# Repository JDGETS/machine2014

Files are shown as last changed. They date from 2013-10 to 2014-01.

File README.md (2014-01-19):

Machine des Jeux de Génie 2014
===========

Le logiciel de la machine est développer entièrement en Python, est exécuté sur un BeagleBone Black avec Ångström et utilise la librairie Adafruit.BBIO pour le contrôle des GPIO/ADC/PWM.

Les sources sont disponible dans /code/src/.

Le camion exécute /code/src/main_camion.py et la trieuse /code/src/main_collector.

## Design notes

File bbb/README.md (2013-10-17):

BeagleBone Black
================

SD card setup:
--------------

We use the Ubuntu Raring 13.04 image from [this site](http://www.armhf.com/index.php/download/)

```
cd /tmp
wget http://s3.armhf.com/debian/raring/bone/ubuntu-raring-13.04-armhf-rootfs-3.8.13-bone20.img.xz
xz -cd ubuntu-raring-13.04-armhf-3.8.13-bone20.img.xz > /dev/*YOURDEVICE*
```
ATTENTION: ne vous trompez pas de device!

C'est possible que `sudo su -` soit necessaire pour la derniere commande.

First Boot:
-----------

1. Figure out the IP address of the device. On the JDG-Machine network, goto http://192.168.1.1/ and look for computer named "ubuntu-armhf".
2. Boot the device; you should be able to connect to SSH with username *ubuntu* & password *ubuntu*
3. Do the "Ubuntu Setup" procedure below (only once).

Ubuntu Setup:
-------------

1. Go to `/etc/network/interfaces` and uncomment the wlan0 lines at the bottom. Setup the wifi name (JDG-Machine) and password.
2. Download the Machine 2014 repo: `git clone https://github.com/JDGETS/machine2014.git`
3. $ cd machine2014/bbb
4. $ make install-deps
5. $ install vim and screen from apt-get : sudo apt-get install screen vim
6. copy .bashrc and .screenrc from the scripts folder to the home directory
7. add your public key and copy the authorized_keys to ~/.ssh/ dont forget to commit the changes to authorized_keys
8. copy interfaces file from the script folder to /etc/network/
9. $ git config --global user.email "machine-jdg-2014@googlegroups.com"

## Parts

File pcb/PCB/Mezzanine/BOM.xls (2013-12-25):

Designator | Description | LibRef | Quantity | Value | Supplier Part Number 1 | Supplier Unit Price 1 | Supplier Subtotal 1
C1, C6, C10 | CAP CER 1UF 50V 10% X7R 0805 | Cap-Samsung-CL-50V-1.0uF-0805-10% | 3 | 1.0uF | 1276-1029-1-ND | 0,11 | 0,33
C2, C7, C11 | CAP CER 2.2UF 50V 10% X5R 0805 | Cap-Samsung-CL-50V-2.2uF-0805-10% | 3 | 2.2uF | 1276-2409-1-ND | 0,32 | 0,96
C3, C4, C8 | CAP TANT 100 16V 10% 2917 | Kemet-T491-100uF-16V-700 mOhm | 3 | 100uF | 399-3770-1-ND | 1,68 | 5,04
C5, C9, C12 | CAP CER 2.2UF 16V 10% X7R 0805 | Cap-TDK-CGA-2.2uF-0805 | 3 | 2.2uF | 445-5691-1-ND | 0,35 | 1,05
C13 | CAP CER 0.1UF 100V 10% X7R 0805 | Cap-TDK-CGA-0.1uF-0805 | 1 | 0.1uF | 445-5827-1-ND | 0,21 | 0,21
D1, D2, D3, D4, D5, D6, D7, D8, D9, D10, D15, D16, D17, D18 | DIODE GEN PURPOSE 1000V 1A SMA | S1M-13-F | 14 | SMA | S1M-FDICT-ND | 0,13 | 1,82
D11, D12 | LED 630NM RED WTR CLR 0805 SMD | LED-Red-2mA-lowBrigthness-0805 | 2 | red | 511-1292-1-ND | 0,52 | 1,04
D13, D14, D19, D20, D21, D22, D23, D24, D25, D26, D27, D28, D29, D30, D31, D32, D33, D34, D35, D36, D37, D38, D39 | LED SMARTLED GREEN 570NM 0603 | LED-Green-2mA-lowBrigthness-0603 | 23 | 3.92 mcd | 475-2709-1-ND | 0,21 | 4,83
D40 | DIODE GEN PURP 200V 10A DO214AB | MicroCommercial-S10D-TP-10A-1.2V | 1 | 1.2V@10A | S10D-TPMSCT-ND | 0,7 | 0,7
D41 | Led Green 0805 Low Brightness - 10mA | LED-Green-lowBrigthness-0805 | 1 | 6mcd | 160-1179-1-ND | 0,39 | 0,39
F1 | FUSE 2.5A 125V 1206 FAST C1Q | Fuse-1206-BelFuse-Fast-C1Q-2.5A | 1 | 2.5A | 507-1081-1-ND | 0,35 | 0,35
F2, F3 | FUSE SLOW 32VDC 3A 1206 | Fuse-1206-Bourns-Slow-SinglFuse_SF-1206S-3A | 2 | 3A | SF-1206S300-2CT-ND | 0,71 | 1,42
F4, F5 | FUSE SLOW 24VDC 5A 1206 | Fuse-1206-Bourns-Slow-SinglFuse_SF-1206S-5A | 2 | 5A | SF-1206S500-2CT-ND | 0,71 | 1,42
J1, J2, J3, J4, J5, J6, J7, J8, J9, J10, J11, J12, J13, J14, J15, J16, J17, J18, J19, J20, J21, J22, J23, J24, J25, J26, J27, J28, J29, J30, J31, J32, J33, J34, J35, J36, J37, J38, J39, J40, J41, J42, J43, J44, J45, J46, J47, J48, J49, J50, J51, J52, J53, J54, J55, J56, J57, J58, J59, J60, J61, J62, J63, J64, J65, J66, J67, J68, J69, J70, J71, J72, J73, J74, J75, J76, J77, J78, J79, J80, J81, J82, J83, J84, J85, J86, J87, J88, J89, J90, J91, J92, J93, J94, J95, J96, J97, J98, J99, J100, J101, J102, J103, J104 | RES 0.0 OHM 1/8W JUMP 0805 | Jumper-0805 | 104 | 0 | RMCF0805ZT0R00CT-ND | 0,01 | 1,1
L1 | INDUCTOR POWER 3.3UH 2.15A 0403 | Ind-Bourns-SRN403-20%-3.3uH | 1 | 3.3uH | SDR0403-3R3MLCT-ND | 0,53 | 0,53
P1, P2 |  | Header-0.100-Generic-2x23 | 2
P3, P4 | CONN HEADER 5POS .100" STR TIN | Header-0.100-Vertical-Lock-1X5 | 2 | 5 pins | WM8216-ND | 1,34 | 2,68
P5, P6, P7 | CONN HEADER 4POS .100" STR TIN | Header-0.100-Vertical-Lock-1X4 | 3 | 4 pins | WM8215-ND | 1,29 | 3,87
P8, P9, P10, P11, P12, P13, P14, P15, P16, P17, P18, P19, P20, P21, P30, P31, P32, P33, P34, P36 | CONN HEADER 2POS .100" STR TIN | Header-0.100-Vertical-Lock-1X2 | 20 | 2 pins | WM8213-ND | 0,94 | 18,78
P22, P23, P24, P25, P26, P27, P28, P29 | CONN HEADER 3POS .100" STR TIN | Header-0.100-Vertical-Lock-1X3 | 8 | 3 pins | WM8214-ND | 1,23 | 9,84
P35 | TERM BLOCK HDR 5.08MM 4POS PCB | ConnBlock-200mils-RightAngle-THT-4pos | 1 | 4 Pos | OSTOQ045451
Q1, Q2, Q3, Q4, Q5, Q6, Q7, Q8, Q9, Q10, Q11, Q12, Q13, Q14, Q15, Q16, Q17, Q18, Q19, Q20, Q21, Q22, Q23, Q24, Q25, Q26, Q27, Q28, Q29, Q30 | MosFET Channel-N SOT-23-3 3.3A | 2N7002 | 30 | Channel N | SI2304DDS-T1-GE3CT-ND | 0,37 | 11,24
R1, R2, R7, R8, R11, R12, R13, R14, R15, R16, R17, R18, R21, R22, R27, R28, R31, R32, R39, R40, R41, R42, R43, R44, R51, R52, R53, R54, R55, R56, R57, R58, R59, R60, R61, R62, R63, R82, R83, R84, R85, R89, R90, R92, R93 | RES 10K OHM 1/8W 5% 0805 SMD | Yagao-RC0805-10k | 45 | 10k | 311-10KARCT-ND | 0,02 | 0,68
R3, R64, R65, R66, R67, R68, R69, R70, R71, R72, R73, R74, R75, R76, R77, R78, R79, R80, R81 | RES 1.6K OHM 1/8W 5% 0805 SMD | Yagao-RC0805-1.6k | 19 | 1.6k | 311-1.6KARCT-ND | 0,02 | 0,38
R4 | RES 8.06K OHM 1/8W 1% 0805 SMD | Yagao-RC0805-1%-8.06k | 1 | 8.06k | 311-8.06KCRCT-ND | 0,12 | 0,12
R5 | RES 21.0K OHM 1/8W 1% 0805 SMD | Yagao-RC0805-1%-21k | 1 | 21k | 311-21.0KCRCT-ND | 0,12 | 0,12
R6 | RES 2.7K OHM 1/8W 5% 0805 SMD | Yagao-RC0805-2.7k | 1 | 2.7k | 311-2.7KARCT-ND | 0,12 | 0,12
R9, R10, R19, R20, R25, R26, R29, R30 | RES 100 OHM 1/8W 5% 0805 SMD | Yagao-RC0805-100 | 8 | 100 | 311-100ARCT-ND | 0,12 | 0,96
R23 | RES 5.1K OHM 1/8W 5% 0805 SMD | Yagao-RC0805-5.1k | 1 | 5.1k | 311-5.1KARCT-ND | 0,12 | 0,12
R24 | RES 732 OHM 1/8W 1% 0805 SMD | Yagao-RC0805-1%-732 | 1 | 732 | 311-732CRCT-ND | 0,12 | 0,12
R33, R35, R45, R46, R48, R49 | RES 1.20K OHM 1/8W 1% 0805 SMD | Yagao-RC0805-1%-1.2k | 6 | 1.2k | 311-1.20KCRCT-ND | 0,12 | 0,72
R34, R36, R37, R38, R47, R50 | RES 1.78K OHM 1/8W 1% 0805 SMD | Yagao-RC0805-1%-1.78k | 6 | 1.78k | 311-1.78KCRCT-ND | 0,12 | 0,72
R86, R87 | RES 11K OHM 1/8W 5% 0805 SMD | Yagao-RC0805-11k | 2 | 11k | 311-11KARCT-ND | 0,12 | 0,24
R88, R91 | RES 750 OHM 1/8W 5% 0805 SMD | Yagao-RC0805-750 | 2 | 750 | 311-750ARCT-ND | 0,12 | 0,24
R94 | RES 1.0K OHM 1/8W 5% 0805 SMD | Yagao-RC0805-1k | 1 | 1k | 311-1.0KARCT-ND | 0,12 | 0,12
SW1 | SWITCH TACTILE SPST-NO 0.05A 12V | TactSwitch-SMD-Vertical-GullWing-6x6 | 1 |  | 450-1759-1-ND | 0,28 | 0,28
U1 | IC BRIDGE DRIVER PAR 15MULTIWATT | L298N | 1 |  | 497-1395-5-ND | 5,26 | 5,26
U2, U7, U8 | REG SW 2.5-12.6V 3A HORZ T/H | PTN78060WAH | 3 | 2.5 ~ 12.6 V | 296-20523-ND | 24,55 | 73,65
U3, U4 | IC OPAMP GP 1MHZ RRO 14SOIC | MCP6L04T | 2 | ±6V | MCP6L04T-E/SLCT-ND | 0,54 | 1,08
U5, U6 | Pololu 4 phase stepper driver 1/32 step | Pololu-DRV8825-BiPolar-HighCurrent | 2 | 1.5A /phase | 2133
U9 | IC DEBOUNCER SWITCH DUAL SOT23-6 | MAX6817 | 1 | 2 Channels | MAX6817EUT+TCT-ND | 5,91 | 5,91
U10 | OPTOCOUPLER TRANS 5KVRMS 8SMD | LTV-827S-TA1 | 1 |  | 160-2040-1-ND | 0,62 | 0,62

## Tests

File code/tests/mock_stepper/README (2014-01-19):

PYTHONPATH=$PYTHONPATH:../../src/ python stepper_mock.py

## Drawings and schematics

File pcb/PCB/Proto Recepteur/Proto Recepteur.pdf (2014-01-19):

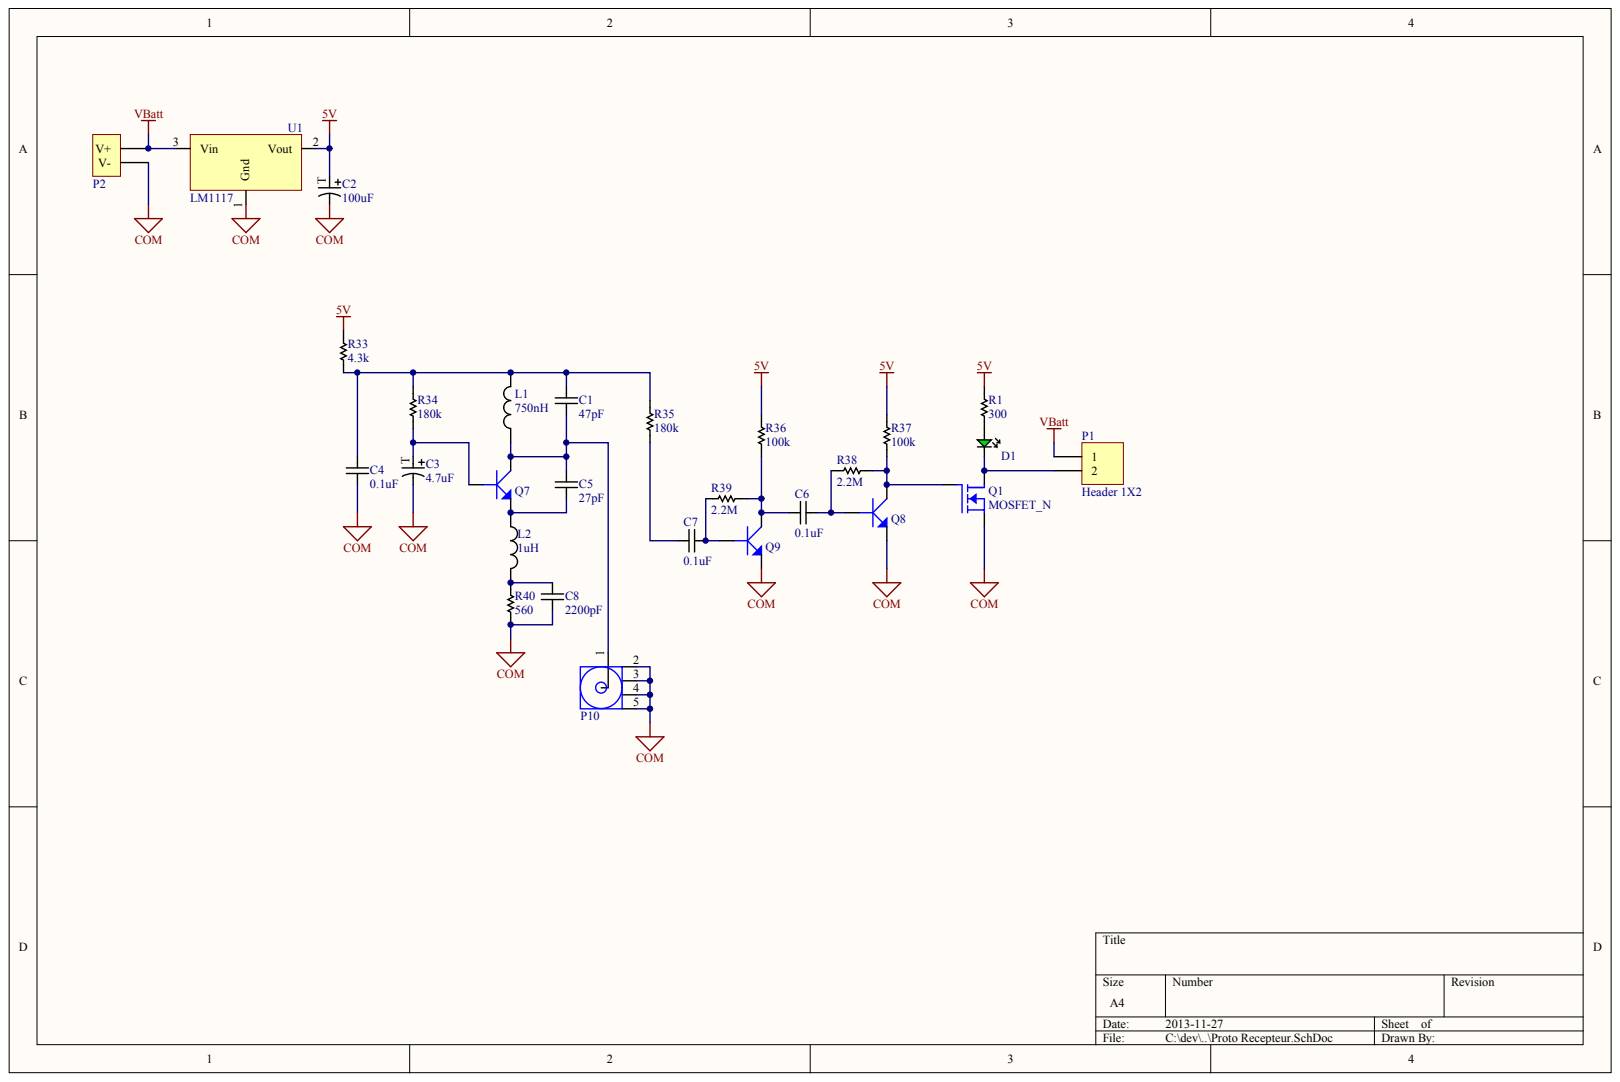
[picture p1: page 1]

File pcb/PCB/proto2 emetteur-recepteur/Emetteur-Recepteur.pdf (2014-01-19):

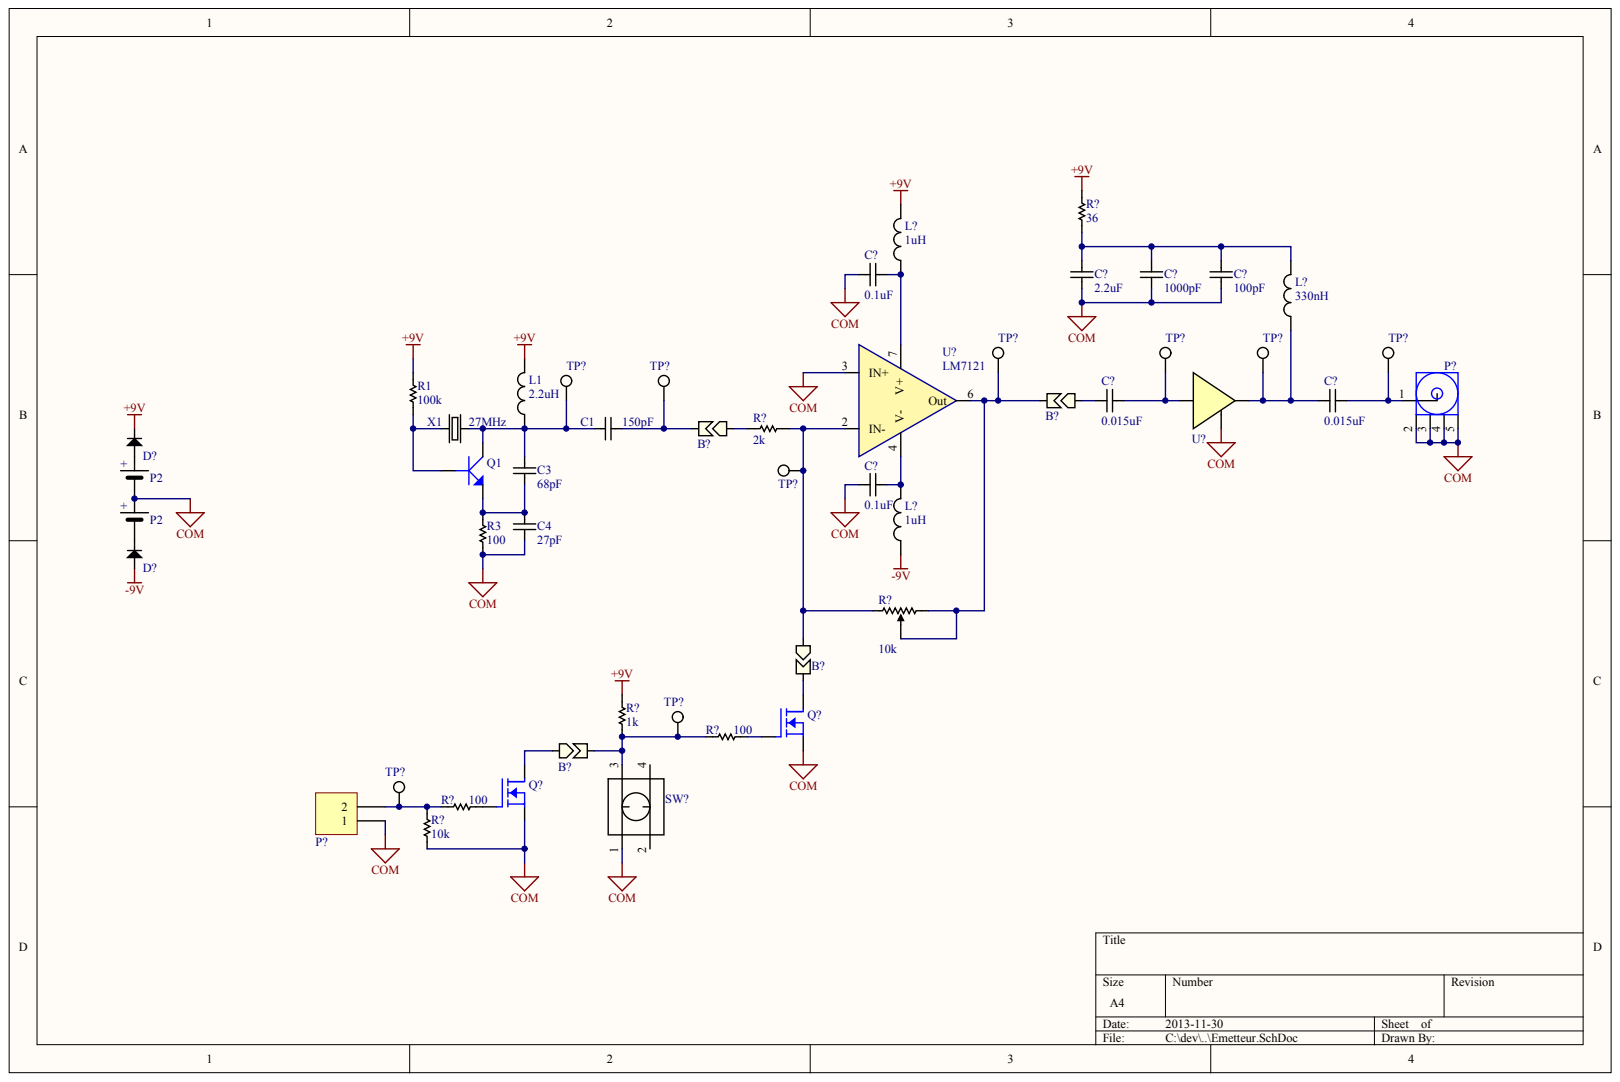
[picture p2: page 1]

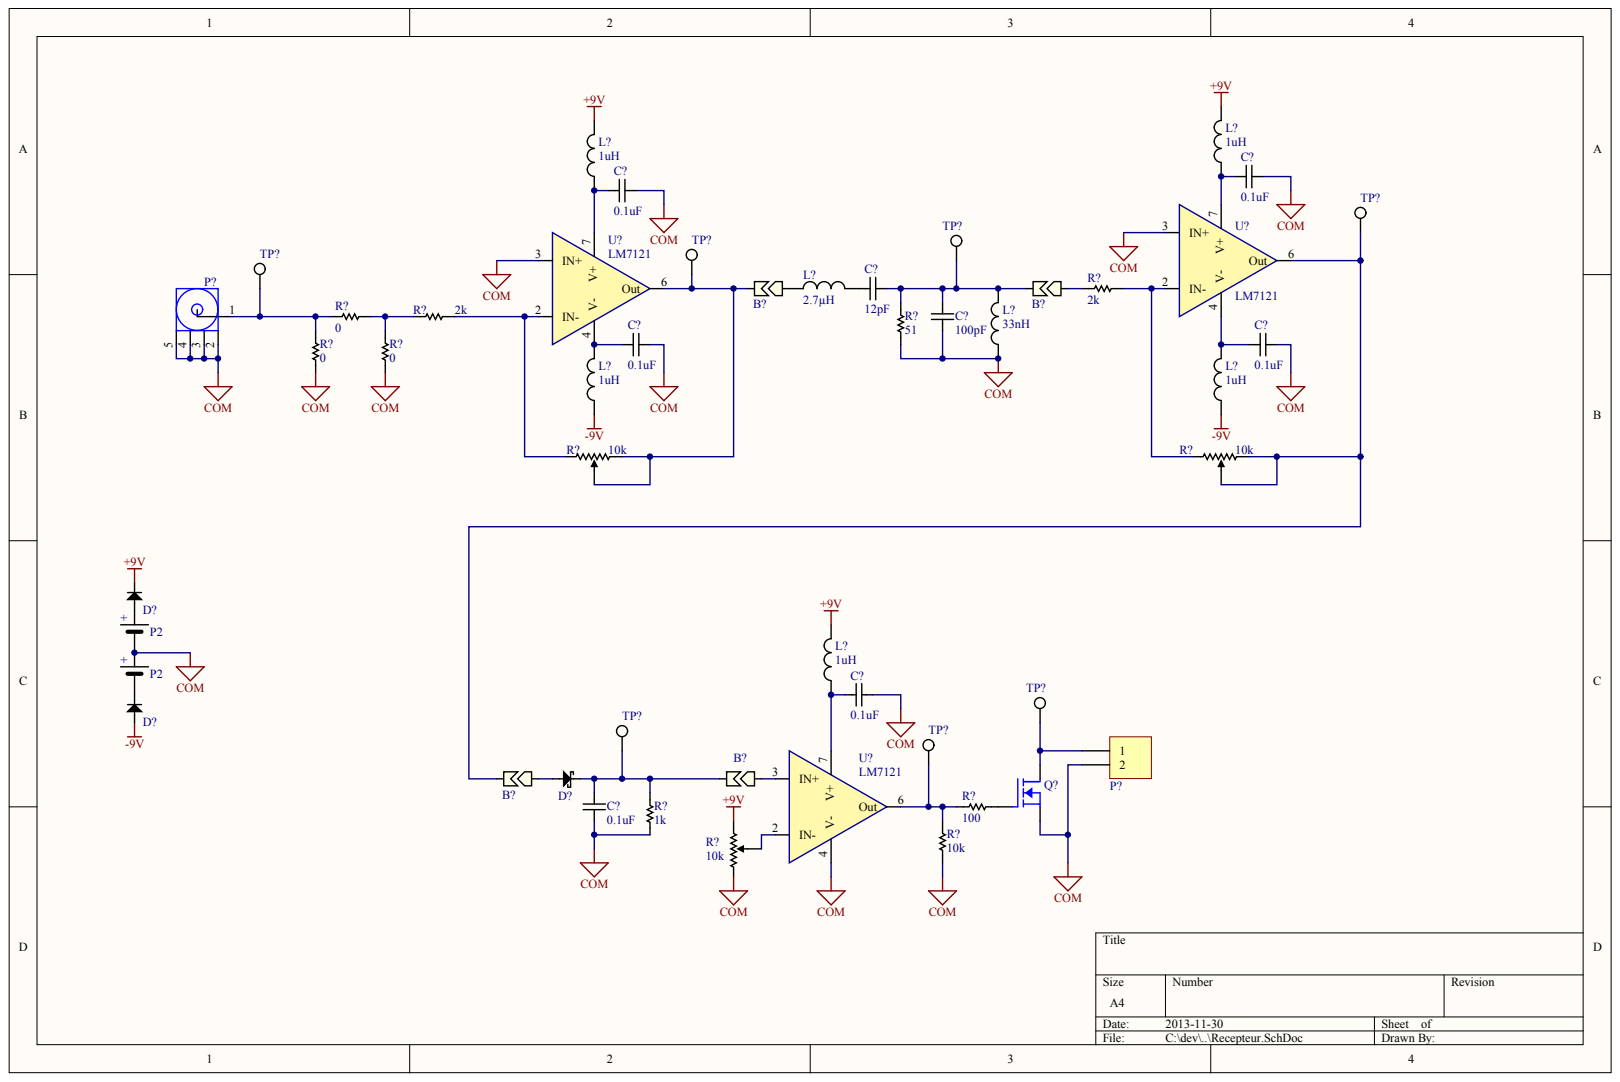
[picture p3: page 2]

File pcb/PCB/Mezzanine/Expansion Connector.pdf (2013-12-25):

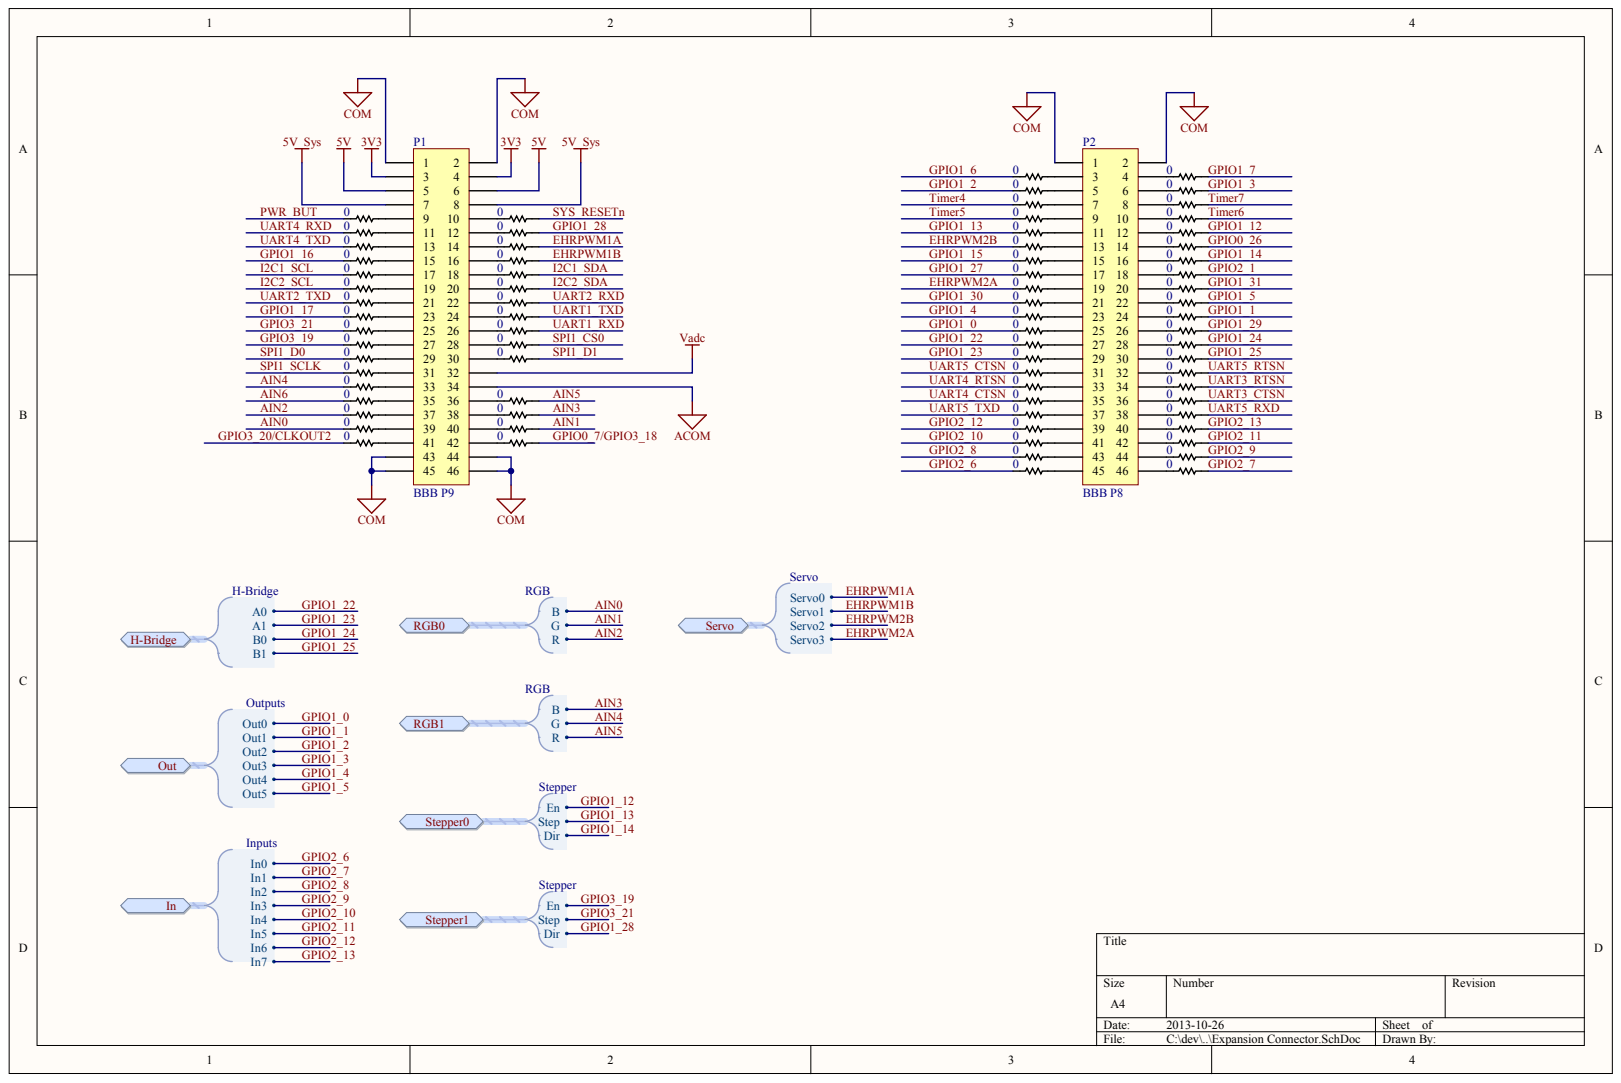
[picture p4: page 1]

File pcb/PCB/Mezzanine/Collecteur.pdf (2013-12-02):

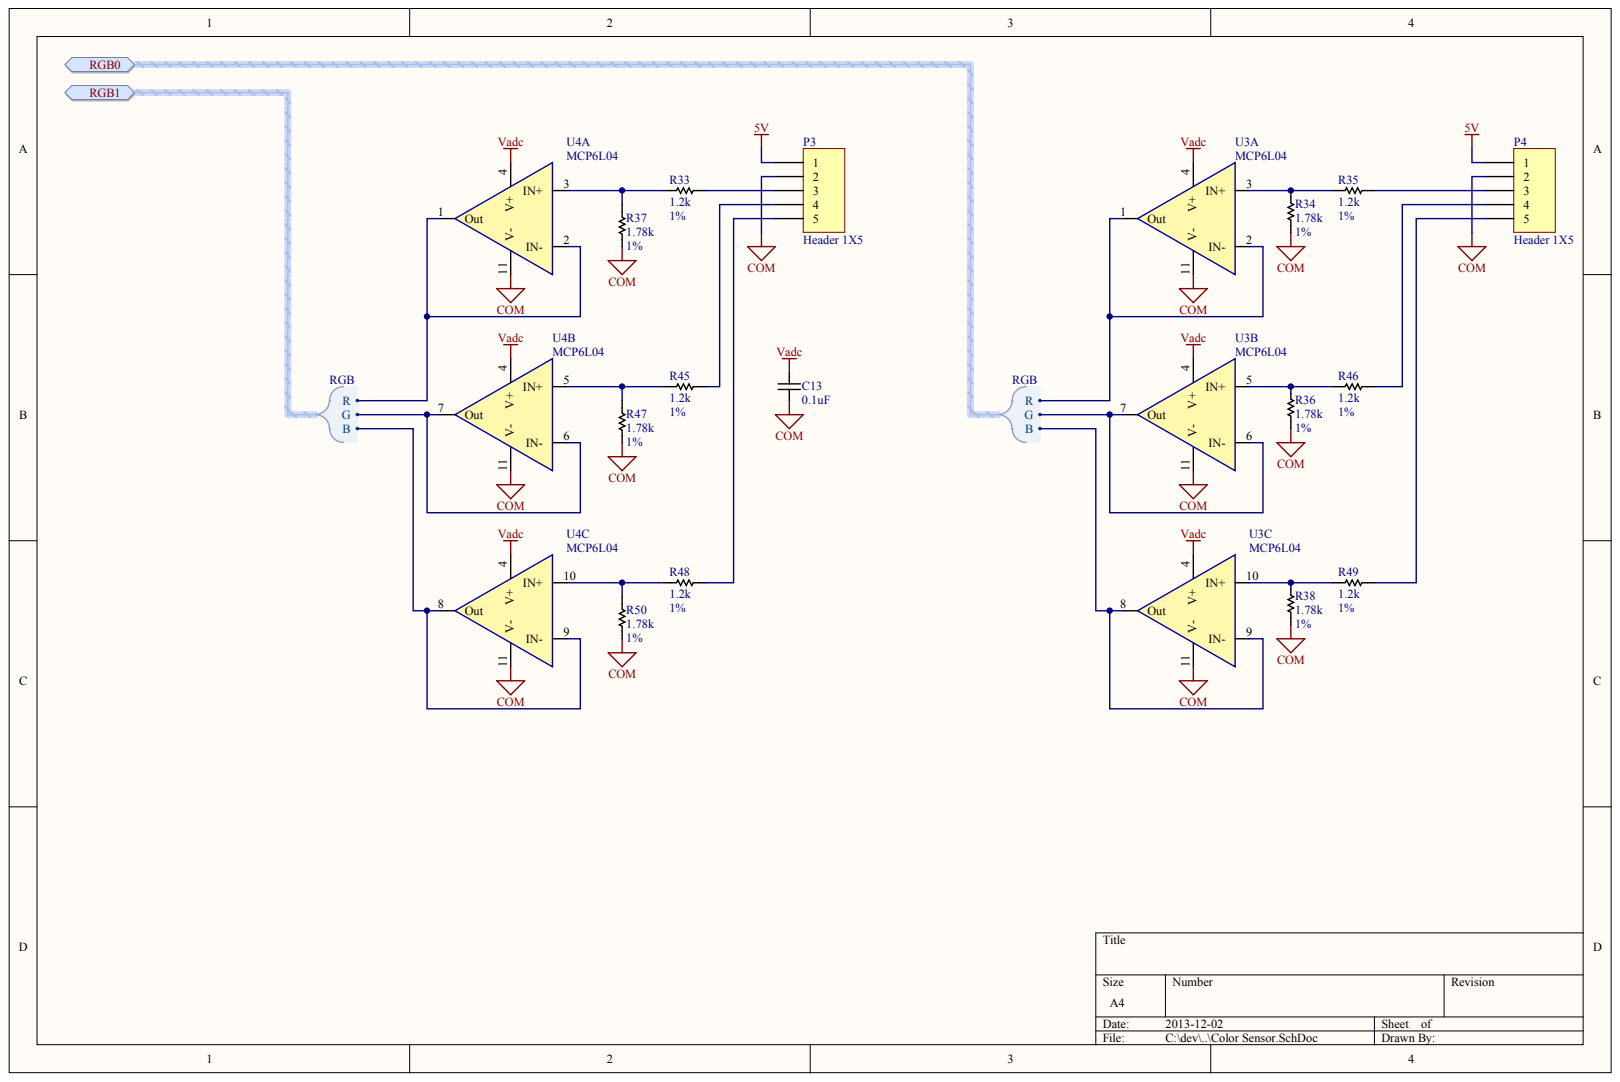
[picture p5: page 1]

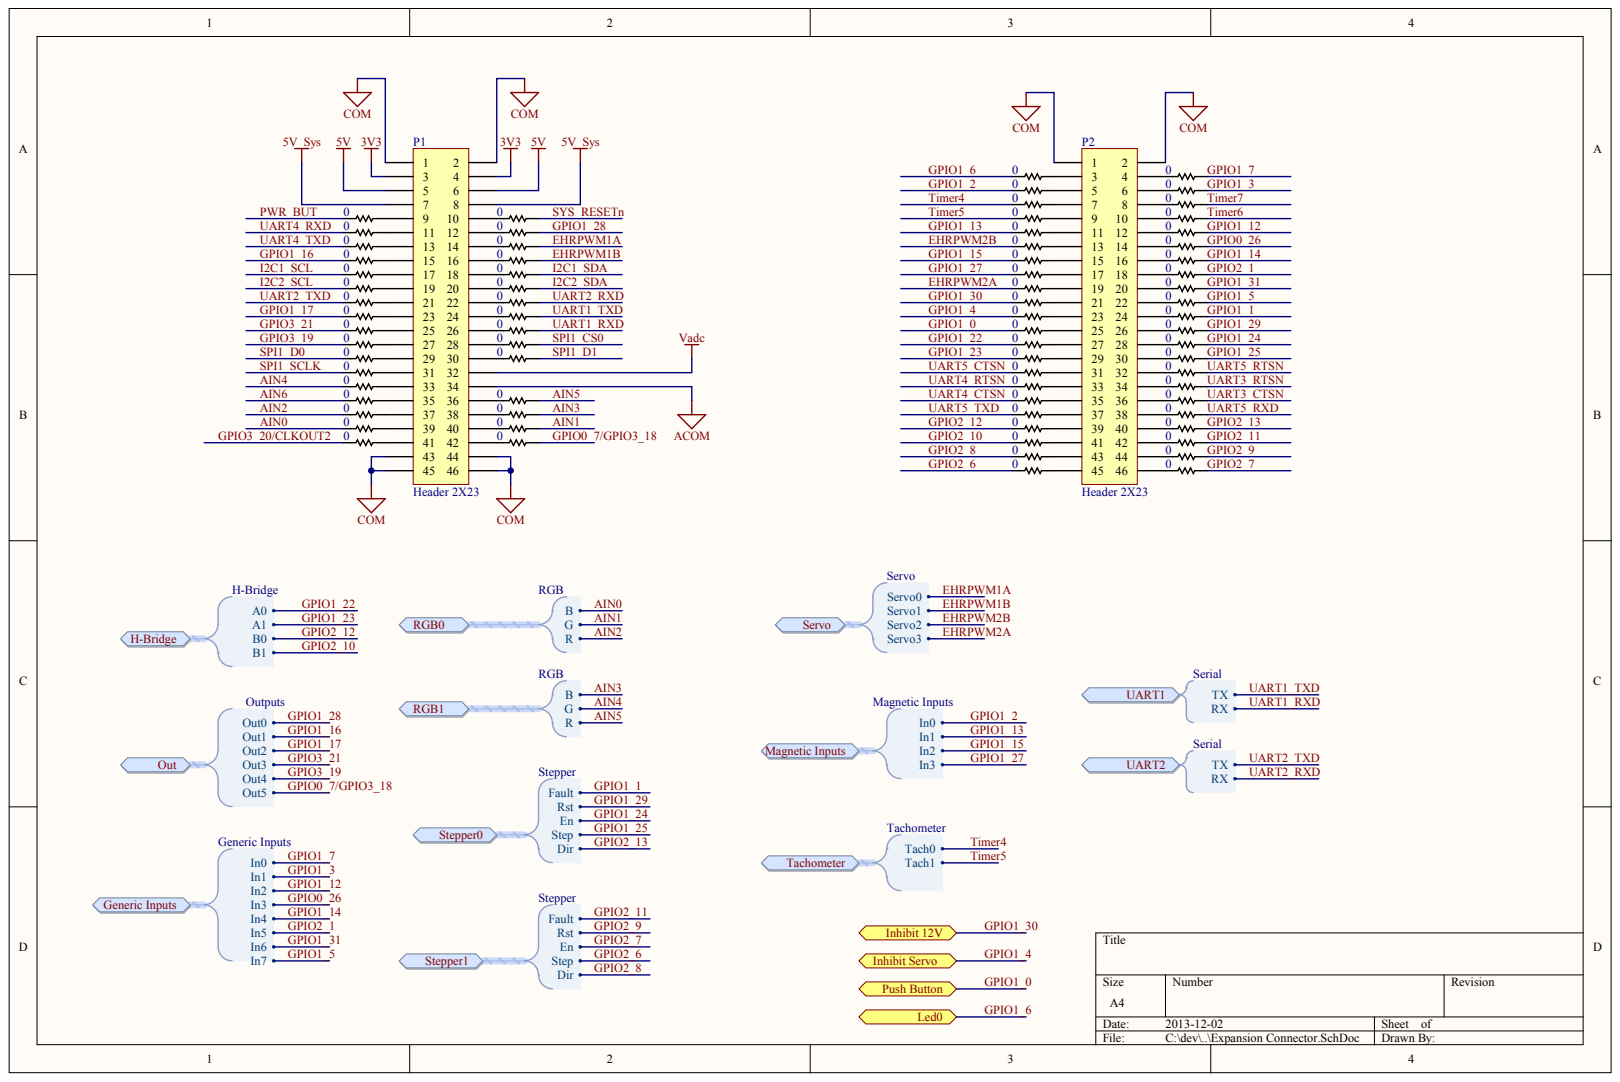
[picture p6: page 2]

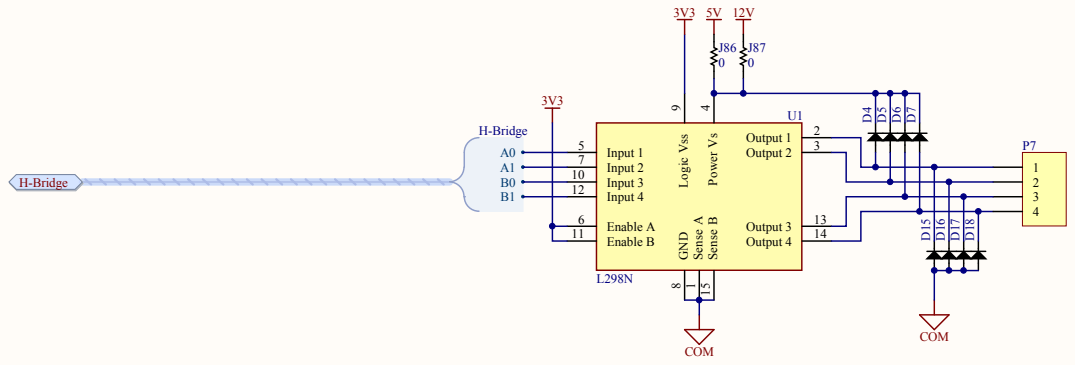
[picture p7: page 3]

Output 1 Input 1 Output 2 Input 2 3 10 Input 4 12 Input Enable A

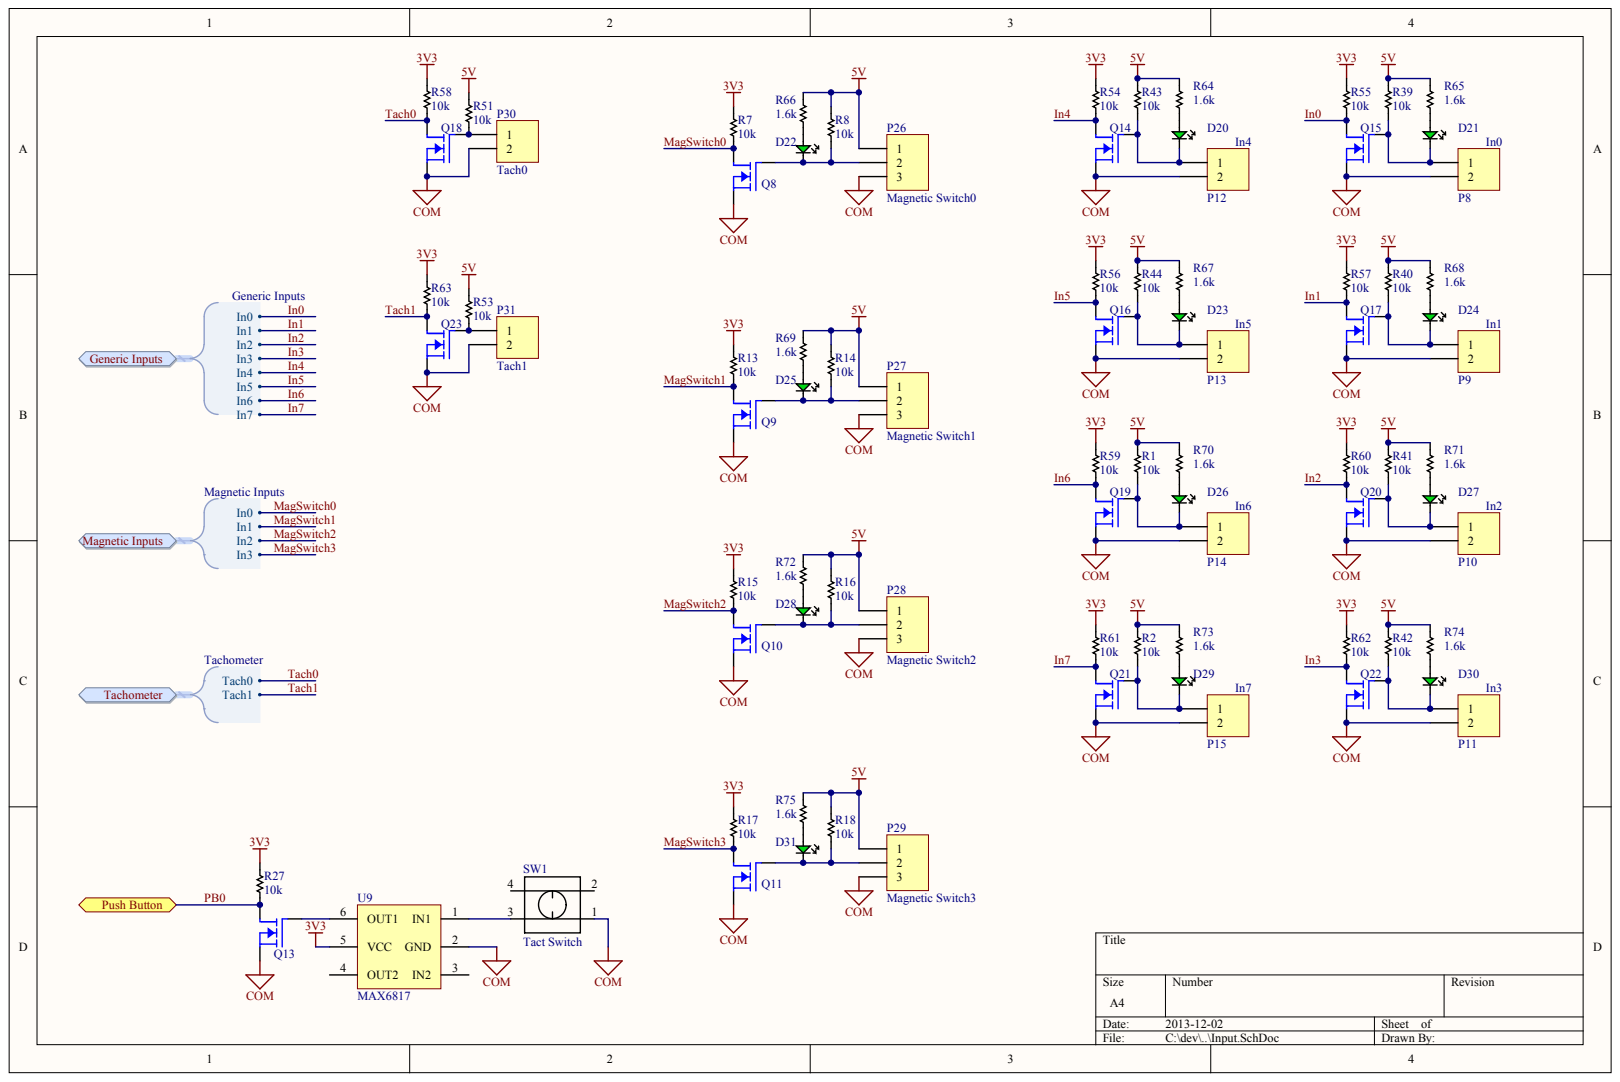
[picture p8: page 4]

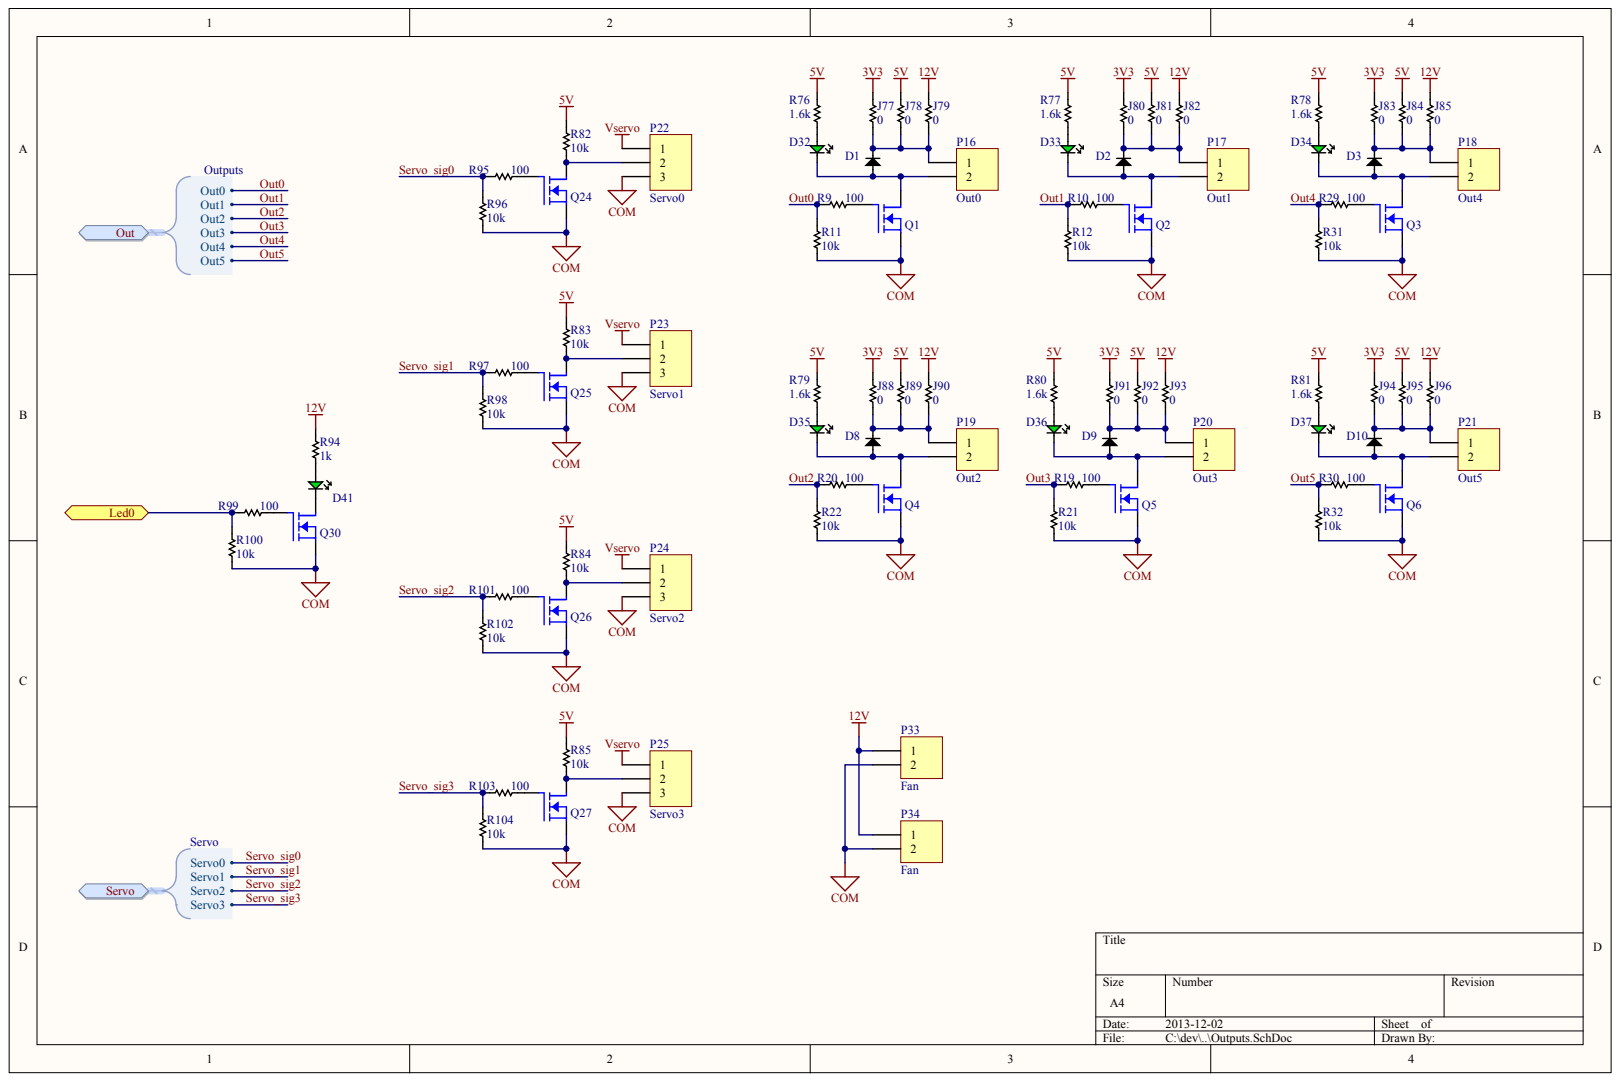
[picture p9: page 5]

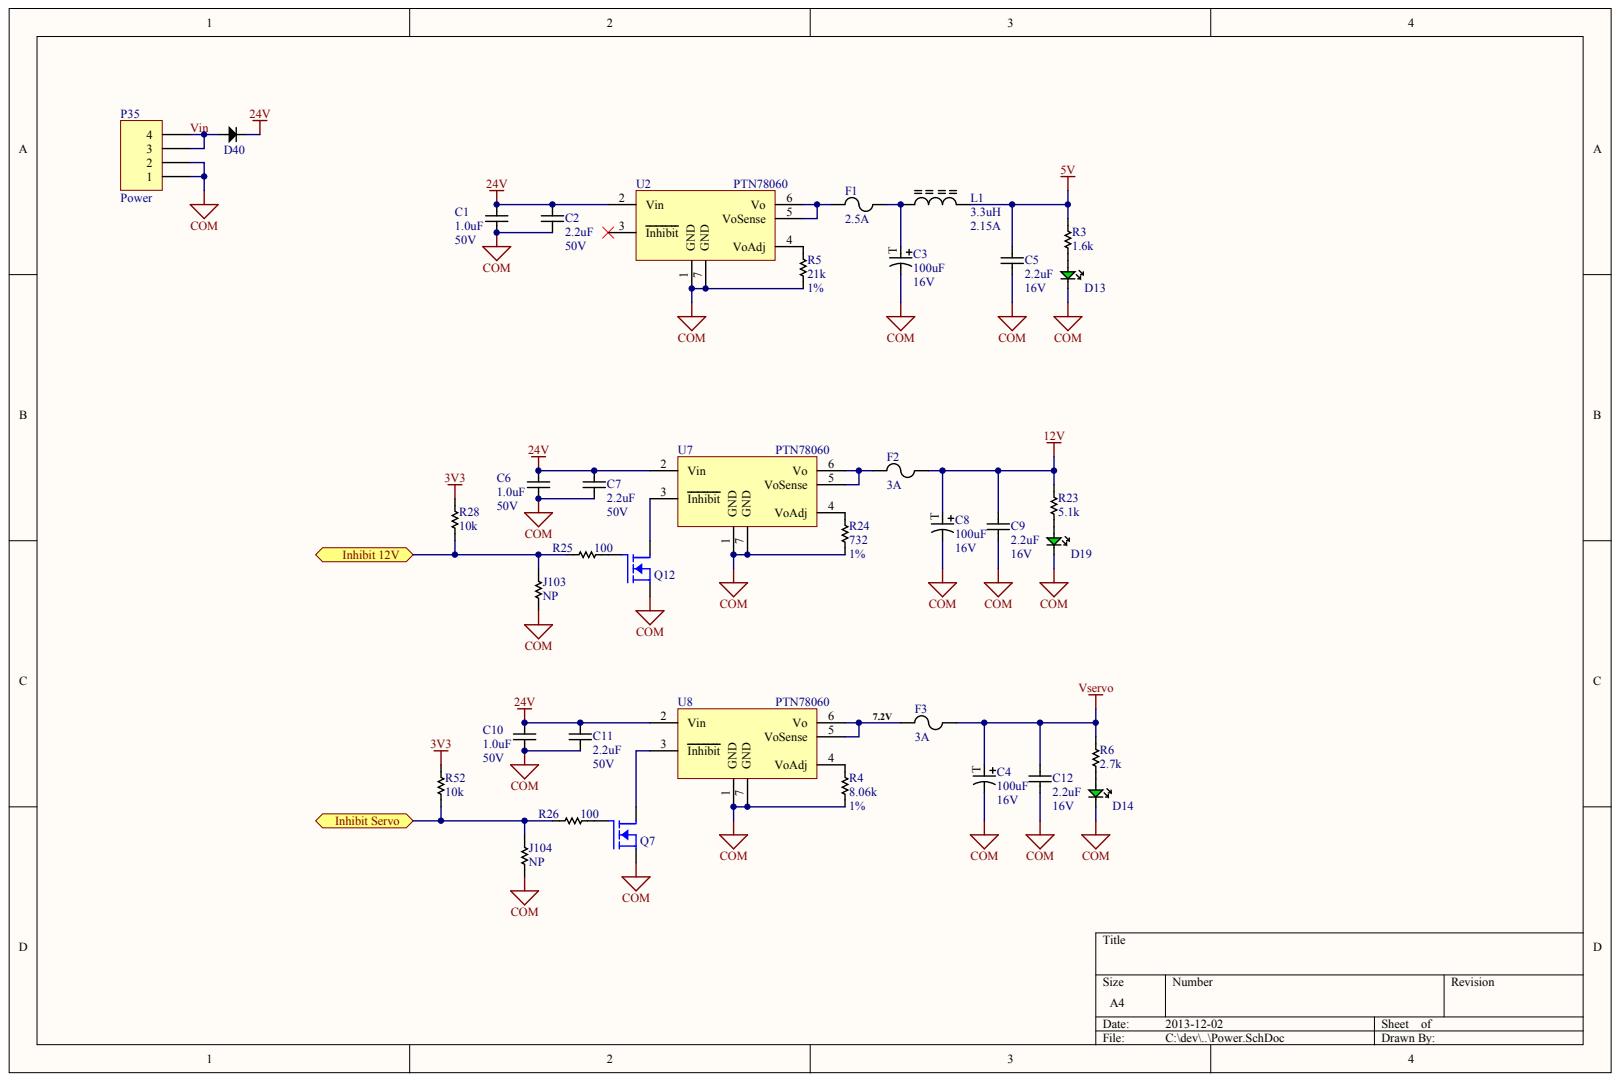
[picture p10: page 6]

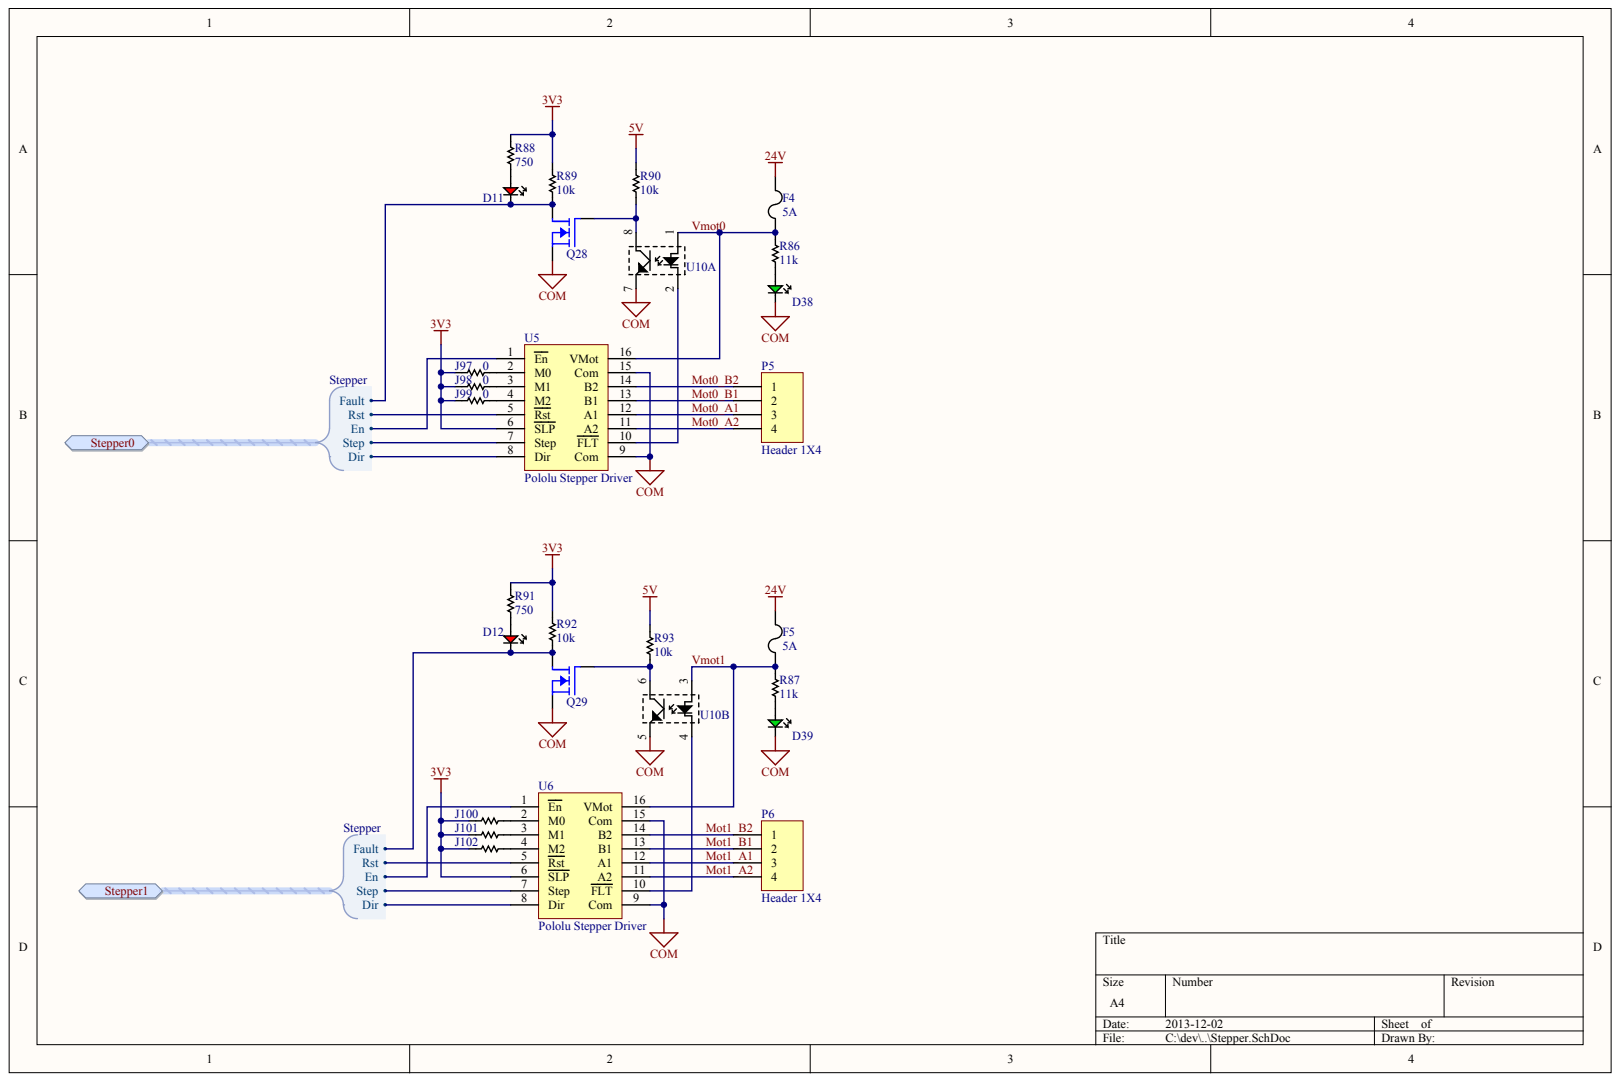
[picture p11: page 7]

SLP Step | Mot0_A 1

Mot0_A 2

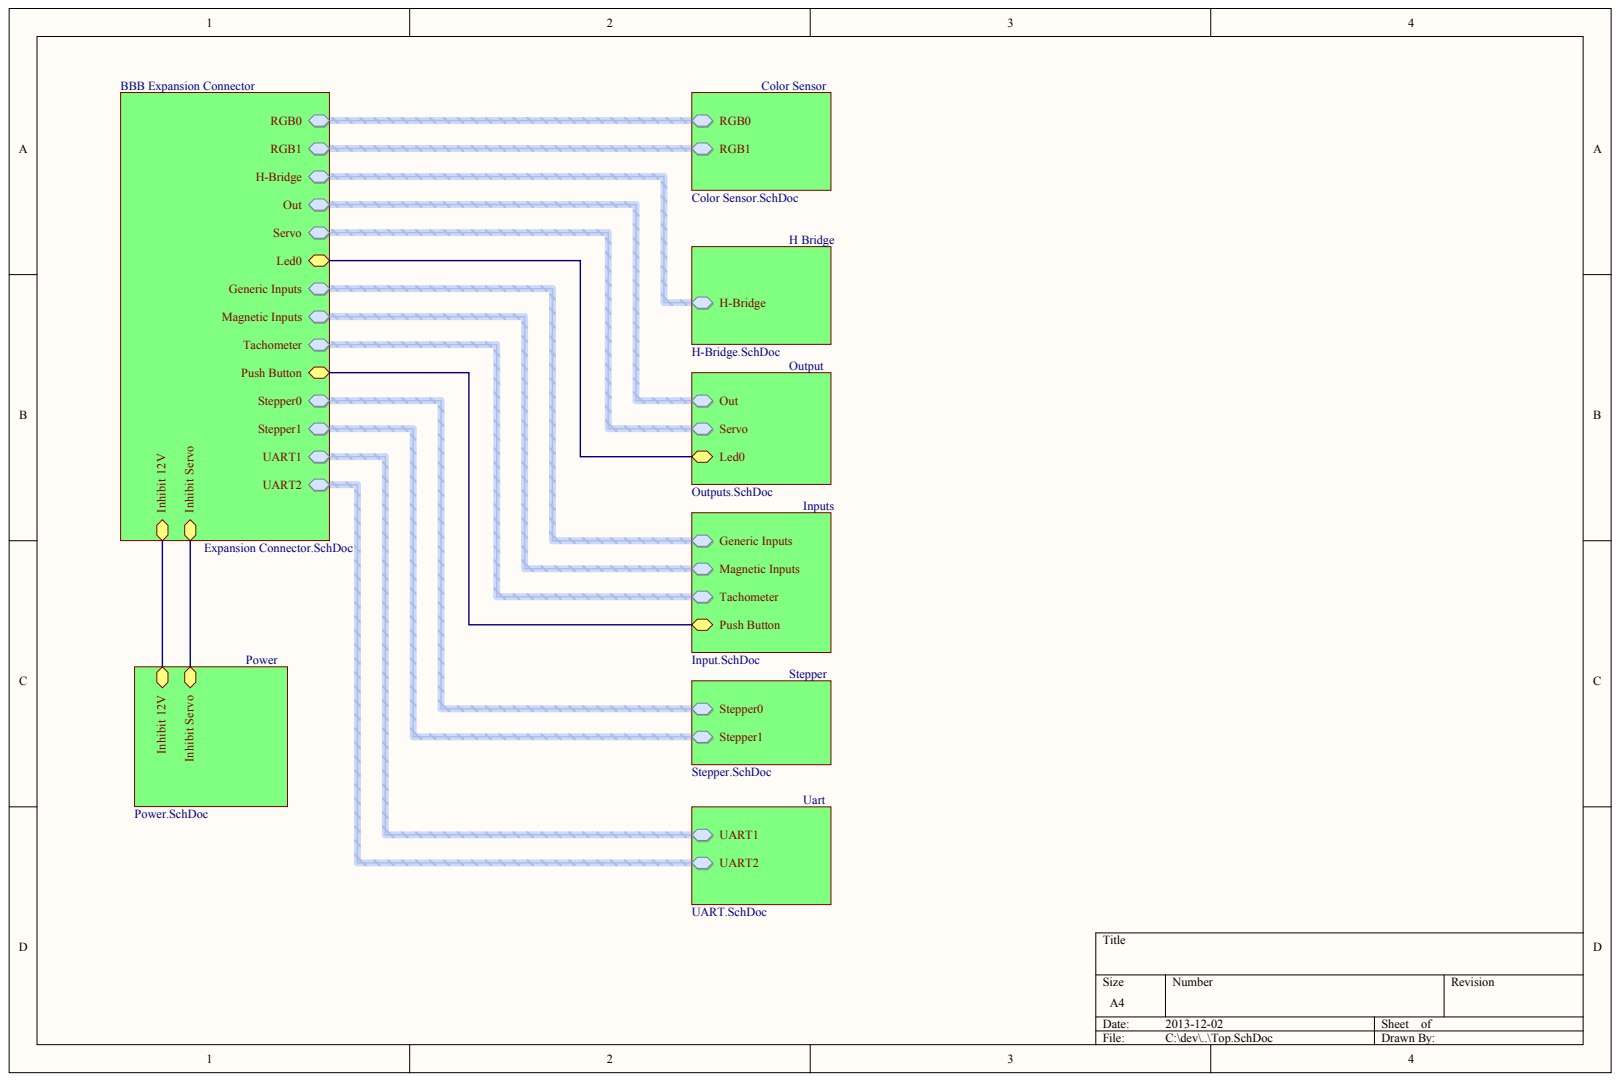
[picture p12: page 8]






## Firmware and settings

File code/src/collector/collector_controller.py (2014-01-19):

from lib.component import Component
from device import Piston, Switch
from device.magnetic_switch import MagneticSwitch
from sorter import Sorter
from vacuum_shaker import VacuumShaker
from lib import config
from lib.logger import Logger
import time

class CollectorController(Component):

    WAIT_TIME_GATE = 1.5
    WAIT_TIME_FOOT = 2.0
    WAIT_TIME_DUMP_BALLS = 1.5
    MAX_BALLS_PER_ROUND = 20
    MAX_DELAY_BETWEEN_BALLS = 2.0
    MAX_DELAY_CYCLE = 30.0
    START_COLLECT = 'start_collect_switch'
    GATE = 'gate_servo'
    FOOT_UP = 'collector_foot_up'
    FOOT_DOWN = 'collector_foot_down'

    def __init__(self, collector):
        super(CollectorController, self).__init__(self.state_wait_init)
        print "[CollectorController.__init__]"
        self.sorter = collector.sorter
        self.rail = collector.rail
        self.vacuum_shaker = collector.vacuum_shaker
        self.start_collect_switch = Switch(**config.devices[self.START_COLLECT])
        self.foot_up_switch = MagneticSwitch(**config.devices[self.FOOT_UP])
        self.foot_down_switch = MagneticSwitch(**config.devices[self.FOOT_DOWN])
        self.gate = Piston(**config.devices[self.GATE])

    def stop(self):
        print "[CollectorController.stop] Stop controller"
        self.gate.stop();

    def state_wait_init(self):
        print "[CollectorController.state_wait_init]"

        #Initialiser la position du collecteur,
        self.rail.slide_to_home()

        while self.rail.is_moving():
            yield

        self.rail.slide_to_wait_for_sorting_position()

        while self.rail.is_moving():
            yield

        # Wait for start switch from collector
        if not self.vacuum_shaker.load_tank_switch.is_pressed():
            self.vacuum_shaker.load_tank_switch.wait_pressed()
        print "[CollectorController.state_wait_init] load_tank_switch pressed"

        # Wait for start switch from truck
        if not self.start_collect_switch.is_pressed():
            self.start_collect_switch.wait_pressed()
        print "[CollectorController.state_wait_init] start_collect_switch pressed"

        self.vacuum_shaker.is_init = True

        Logger().start_new_cycle() #Start first cycle here

        self.gate.push();

        yield self.state_push_truck_home

    def state_push_truck_home(self):
        print "[CollectorController.state_push_truck_home]"
        self.rail.slide_to_home()

        while self.rail.is_moving():
            yield

        yield self.state_wait_sorter

    def state_push_truck_away(self):
        print "[CollectorController.state_push_truck_away]"
        self.rail.slide_to_away()

        while self.rail.is_moving():
            yield

        Logger().end_current_cycle()
        self.vacuum_shaker.wait_balls()

        yield self.wait( self.WAIT_TIME_DUMP_BALLS, self.state_push_truck_home)

    def state_push_truck_standby(self):
        print "[CollectorController.state_push_truck_standby]"
        self.rail.slide_to_wait_for_sorting_position()

        while self.rail.is_moving():
            yield

        yield self.state_wait_truck_foot

    def ready_to_drop_balls(self):
        balls = self.sorter.get_ball_count()
        last_ball_time = self.sorter.get_last_ball_time()
        cycle_time = self.vacuum_shaker.last_button_push

        done = balls >= self.MAX_BALLS_PER_ROUND
        halfway_done = balls >= self.MAX_BALLS_PER_ROUND/2
        timed_out_ball = int(time.time() - last_ball_time) > self.MAX_DELAY_BETWEEN_BALLS
        timed_out_cycle = int(time.time() - cycle_time) > self.MAX_DELAY_CYCLE

        foot_down = self.foot_down_switch.is_pressed()
        is_home = self.rail.is_home()

        return is_home and foot_down and (done or (halfway_done and timed_out_ball) or (timed_out_cycle and balls > 0))

    def state_wait_sorter(self):
        print "[CollectorController.state_wait_sorter]"

        self.sorter.last_ball_time = time.time()
        self.vacuum_shaker.last_button_push = time.time()

        while not self.ready_to_drop_balls():
            yield

        if self.sorter.get_ball_count() < self.MAX_BALLS_PER_ROUND:
            print "[CollectorController.state_wait_sorter] Timed out. Dumping "+str(self.sorter.get_ball_count())+" balls!"

        Logger().set_current_cycle_ball_count(self.sorter.get_ball_count())

        self.sorter.reset_ball_count()

        yield self.state_open_gate

    def state_open_gate(self):
        print "[CollectorController.state_open_gate]"

        self.gate.pull()

        yield self.wait( self.WAIT_TIME_GATE, self.state_close_gate)

    def state_close_gate(self):
        print "[CollectorController.state_close_gate]"

        self.gate.push()

        yield self.state_push_truck_standby

    def state_wait_truck_foot(self):
        print "[CollectorController.state_wait_truck_foot]"

        while not self.foot_up_switch.is_pressed():
            yield

        yield self.state_push_truck_away

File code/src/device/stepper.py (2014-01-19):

from threading import Thread, Event
import Adafruit_BBIO.GPIO as GPIO
import bbio

#Must be out of the Stepper object. A Thread can only be started once.
# OR:
# """ If you derive a class from threading.Thread you can add a Thread.__init__(self) 
#     at the end of your run method and you'll be able to call start again and it'll 
#     automatically reinitialize itself when it's done. """
def move_thread(kill, pin, steps=-1, default_ramp_step = 2000, min_sleep = 100-15, stop_condition = None):
    """ run this biatch """
    STOP_CONDITION_INTERVAL = 50
    stop_condition = stop_condition or (lambda: False); #Default: No stop conditions
    bbio.pinMode(pin, bbio.OUTPUT)
    step = 0
    ramp_step =  float(default_ramp_step if steps == -1 else min(default_ramp_step, steps))
    ramp_sleep = 100.0
    #ramp_sleep_decrement = ramp_sleep / (ramp_step*ramp_step)
    half_ramp_step = ramp_step/2
    dec = 0
    
    while (step < ramp_step) and not kill.isSet() and \
        (step%STOP_CONDITION_INTERVAL != 0 or not stop_condition()):
        bbio.digitalWrite(pin,bbio.LOW)
        bbio.digitalWrite(pin,bbio.HIGH)
        step +=1
        
        x = (step/ramp_step)
        dec = x*x
        if step > half_ramp_step:
            dec = -(x-1)*(x-1) + 0.5
        bbio.delayMicroseconds( min_sleep + ramp_sleep - 2*dec*ramp_sleep)

    while (step < steps or steps == -1) and not kill.isSet() and \
        (step%STOP_CONDITION_INTERVAL != 0 or not stop_condition()):
        bbio.digitalWrite(pin,bbio.LOW)
        bbio.digitalWrite(pin,bbio.HIGH)
        step +=1
        bbio.delayMicroseconds(min_sleep)

class Stepper(object):
    def __init__(self, pin,direction,reset,enable,ramp_step,min_sleep):
        self.default_ramp_step = ramp_step
        self.min_sleep = min_sleep
        self.pin = pin
        self.killThread = Event()
        self.direction = direction
        self.reset = reset
        self.enable = enable
        self.thread = None
        GPIO.setup(self.reset, GPIO.OUT)
        GPIO.setup(self.enable, GPIO.OUT)
        GPIO.setup(self.direction, GPIO.OUT)
        self.reset_stepper()

    def reset_stepper(self):
        GPIO.output(self.reset, GPIO.LOW)
        GPIO.output(self.reset, GPIO.HIGH)        
        GPIO.output(self.enable, GPIO.LOW)

    #0 or 1 for direction
    def move(self, direction, steps = -1, stop_condition = None):
        print "move %d"%steps
        GPIO.output(self.direction, direction)
        if self.thread and self.thread.is_alive():
            self.stop()
        
        self.reset_stepper()
        self.thread = Thread(target = move_thread, args = (self.killThread, self.pin, steps, self.default_ramp_step, self.min_sleep, stop_condition))
        self.thread.start()
    
    def is_moving(self):
        return self.thread and self.thread.is_alive()

    def stop(self, event = None):
        print "[Stepper.stop] Stop the thread!"
        if self.thread:
            self.killThread.set()
            self.thread.join()
        self.killThread.clear()
        #GPIO.output(self.enable, GPIO.HIGH)

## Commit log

2013-10-14 Importer le code de l'an passé (lib et libcomm) et stuff du collector (basé sur la séquence sur Google Drive).
2013-10-14 Basé sur séquence Camion sur Google Drive. Ne reste plus que l'interaction entre les états du collecteurs et du camion.
2013-10-14 Ajout du stuff pour bouger le camion de gauche à droite (par le Collector). Ajout du SortingModule qui est un refactoring du stuff related au tri (rods et sensors de couleur). Un module de tests pour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
    - Reste à voir si on attend le tri des balles ou pas (si on arrive avant que le tri soit complété)
2013-10-16 added initial (untested) version of LED and Switch wrapper classes
2013-10-16 Refactoring de la simulation parce que je suis pogné chez moi sans BBB et avec rien de mieux à faire.
    Note: Simulation de 10 minutes = 830 balles en 45 aller-retour (sans attendre la fin du tri à chaque aller-retour).
2013-10-16 Implement GPIO limit switch
2013-10-17 Fixed limit switch error
    [switch.py]
2013-10-17 Added dump/ folder for test and/or temporary code & added servo test code
2013-11-04 Add vacuum test and vacuum controller fixes
    [sorter.py]
2013-11-04 Added servo driver
2013-11-05 Added BBB mezzanine board
2013-11-08 Add a small servo test
2013-11-08 Update servo driver
2013-11-14 Updated pcb/Collecteur.pdf
2013-11-19 Final Schematic
2013-11-23 modified: code/src/device/servo.py modified: code/tests/servo.py code/src/device/sort_arm.py
2013-11-27 Updated servo test
2013-11-27 Added config value for servo
2013-11-27 Added color sensor tests
2013-11-27 Fixed color sensor
2013-12-02 Update de shield + Ajout emetteur/recepteur 27Mhz
2013-12-19 debug adc bug
2013-12-19 Compare color distance instead of error threashold
    [color_sensor.py]
2013-12-19 Added back sleep to color_sensor + fixed a couple of bugs
    [color_sensor.py]
2013-12-19 Added a script to calibrate color sensor
2013-12-19 Fixed color_sensor.py mini bugs.
    [color_sensor.py]
2013-12-19 Fixed calibration tool
2013-12-19 Fixed calibration tools
2013-12-19 Fixed comma from color calibration
2013-12-19 Calibrate servo
2013-12-19 Removed color error check
    [color_sensor.py]
2013-12-19 Modifications Collector pour switch Camion.
2013-12-19 Oublié la ,
2013-12-19 Calibrate shaker servo
2013-12-20 Refactored collector switch start
2013-12-20 Moved Switch class to device module
2013-12-20 Add test for switch
2013-12-20 Driver initial du stepper
2013-12-21 move thread
2013-12-21 Fixed sleep in color_sensor
    [color_sensor.py, vacuum_shaker.py]
2013-12-21 Recalibrate servo
2013-12-21 Recalibrate vacuum servo
2013-12-21 Added load tank switch
2013-12-21 Fixed issue with wait ball switch
    [switch.py, vacuum_shaker.py]
2013-12-21 Changements à la sequence de Camion
2013-12-21 Rail Component
2013-12-21 Ajout du controller de collector.py
    Reste Gate dans collector/collector_controller.py et rail à initialiser dans collector.py.
2013-12-21 Added rails to collector.
2013-12-21 Changed Rail's class name
2013-12-21 test rail
2013-12-21 more prints
2013-12-21 Calibrate gate servo
2013-12-22 new configs for new piston vacuum shaker
2013-12-22 ninja noob bug fix
    [collector_controller.py]
2013-12-22 ninja is_moving stepper.
2013-12-22 stepper is_moving
2013-12-23 New configs for gate servo
2013-12-23 Rail en Component (pour gérer à l'interne les déplacements incomplets et tout...).
2013-12-23 ninja new condition de dump
2013-12-23 Code pour le homing a home et away.
    Ninja.
2013-12-23 ninja fix test mores
    [camion.py, stepper.py, switch.py]
2013-12-23 Mathieuuuu.. met des parenthèsessssss!!!!
2013-12-23 config switch
2013-12-23 ninja fix and verbosity much wow
    [camion.py, initialize_camion.py]
2013-12-23 remove bug fix degueu
    [stepper.py, switch.py]
2013-12-23 fix bug magnets...
2013-12-23 n00b bug much tired wow
    [stepper.py]
2013-12-23 refactor the stepper thread code
2013-12-23 take MagneticSwitch to its own file
2013-12-23 Add a switch in truck to place in starting position.
    Incremented stepper speed.
2013-12-24 Revert thread stuff stepper
    [stepper.py]
2013-12-24 La faute de Lavoie
2013-12-25 Ajouté source PCB
    [BOM.xls, Collecteur.PrjPcb, Color Sensor.SchDoc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]
2013-12-26 Tests avec les events sur les switchs.
2013-12-26 Some more edits with bindings
    [camion.py, rail.py]
2013-12-26 servo tests
2013-12-26 bug rail
2013-12-27 mock stepper class to check out the sweet rampup curves
2013-12-27 new switch id
2013-12-27 switchs camion pied
2013-12-27 Switch changements
2013-12-27 modified: code/src/device/stepper.py
2013-12-28 Rail is now in quater step
2013-12-28 hack to ignore noise
    [camion.py]
2013-12-30 pull piston on exit
2013-12-30 Document pin config
2013-12-30 Comment more on camion's switch
2013-12-30 Removed unused switch
2013-12-31 Make sure the foot touch the ground in put_in_start_position
2013-12-31 C'est la faute à EiN
2013-12-31 Added error threshold in color_sensor
    [color_sensor.py]
2013-12-31 Recalibrate gate servo
2013-12-31 Magnetic switch foot down and cycle time out for sortttteer
2013-12-31 blabla new config stepper pied
2013-12-31 Recalibrate piston
2013-12-31 Add switch timeout
2013-12-31 Reset the timeout before waiting for ball
    [collector_controller.py]
2013-12-31 timeout de test pour le vacuum shaker
2014-01-02 INtefrerence fix pour pied camion
    [camion_foot.py]
2014-01-02 Speed up piston
2014-01-02 Replace literal with define
    [rf_receiver.py]
2014-01-02 Fixed foot timeout condition
    [camion_foot.py]
2014-01-03 Wait for load-switch before starting collector
2014-01-03 Fixed switch not working
    [vacuum_shaker.py]
2014-01-04 CHnagements fin de vie du Camion
2014-01-05 sleep in switch
2014-01-06 Clean pwm in case of failure
2014-01-06 Fix switch per FRed's ideas.
    [switch.py]
2014-01-06 Rajouter le code d'arret avec timer de 14 minutes
2014-01-07 Les dernières modification avant la compétition.
2014-01-19 PCB clean
    [BOM.xls, Buttons.SchDoc, Collecteur.PrjPcb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]
